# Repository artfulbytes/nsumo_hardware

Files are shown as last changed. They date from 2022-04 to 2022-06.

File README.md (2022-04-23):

# Nsumo hardware
This repository contains the schematic and PCB design of Nsumo, a mini-class Sumobot (500g 10x10cm),
created in KiCad, and manufactured by JLCPCB. It's a 2-layer PCB with microcontroller MSP430G2553IPW28,
regulators 3.3V (AMS1117-3.3) and 5V (MP2359), two motor drivers TB6612FNG, IR receiver TSP382, and
circuit protection (RS3E075AT).

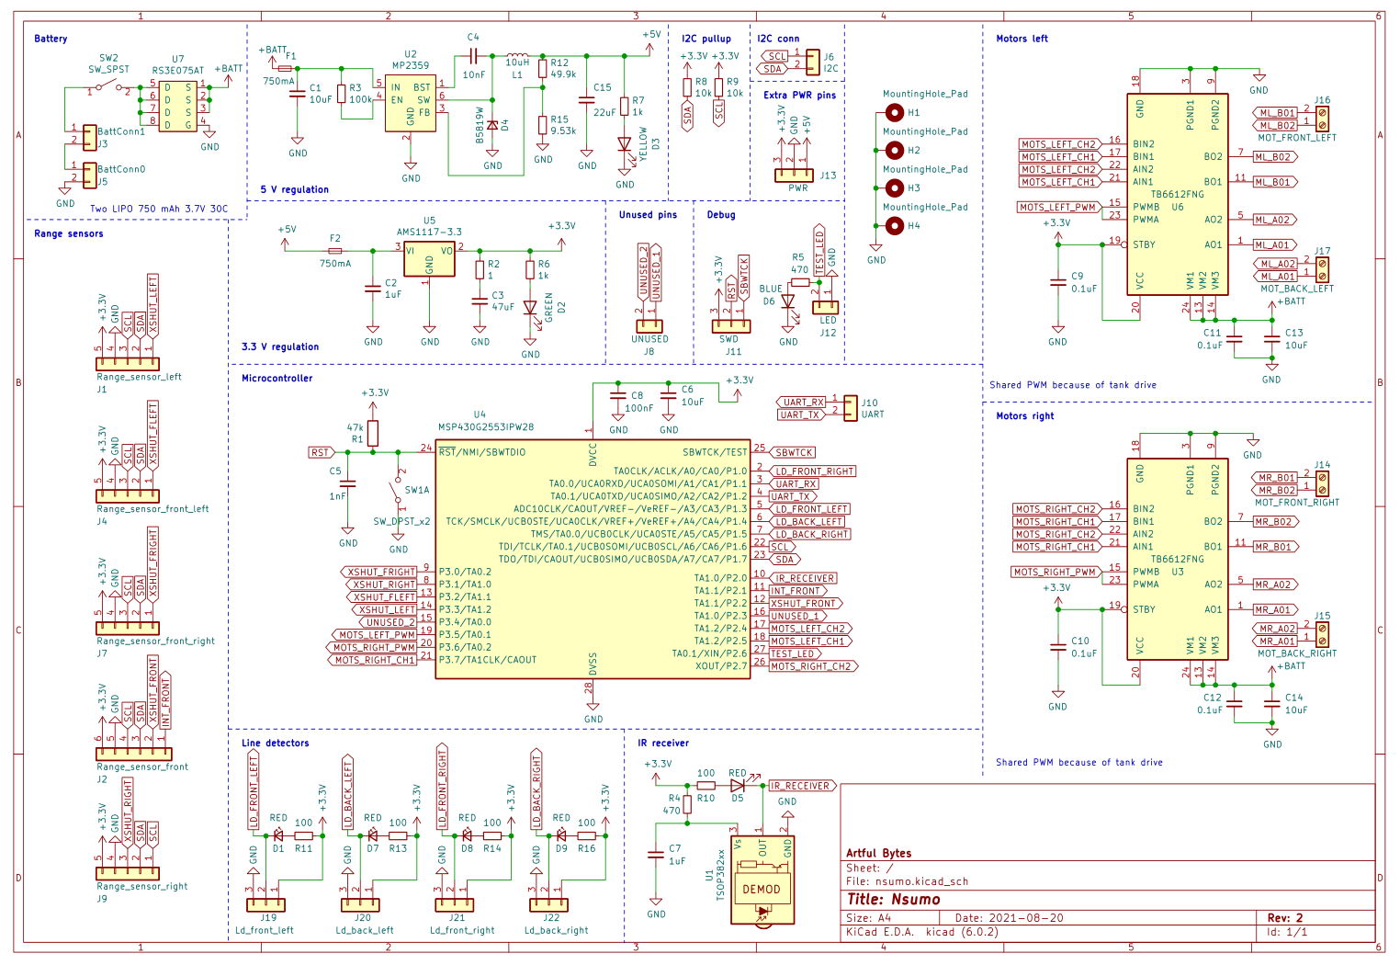
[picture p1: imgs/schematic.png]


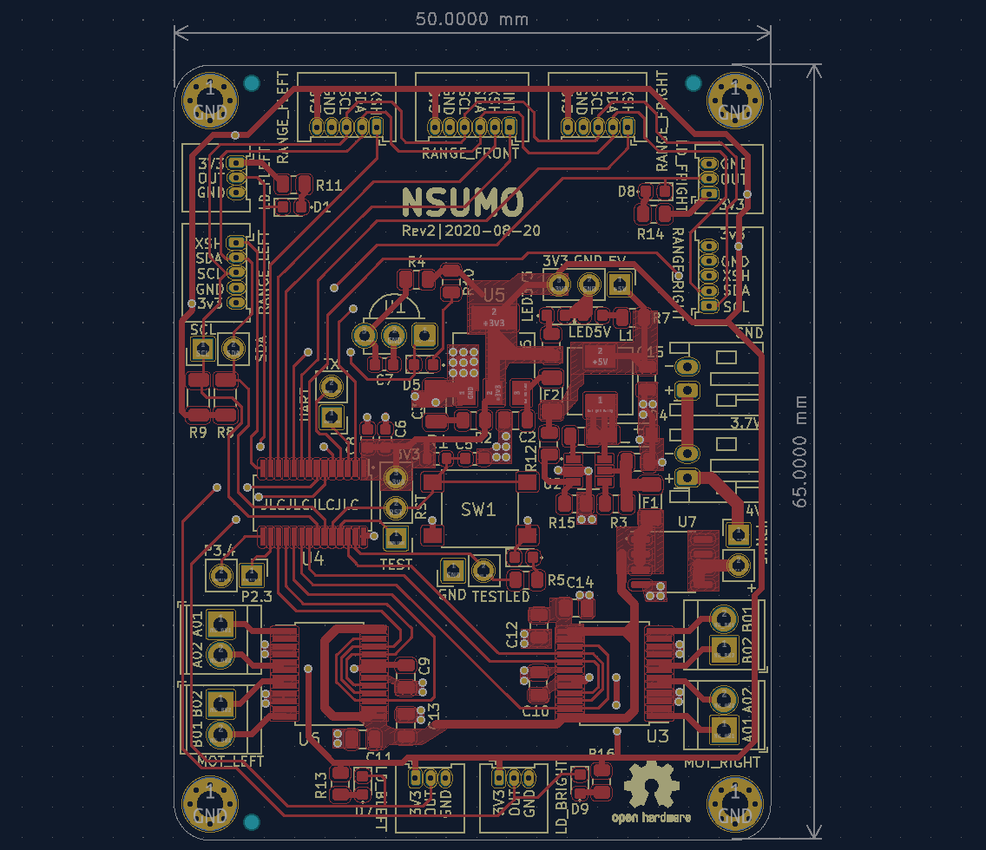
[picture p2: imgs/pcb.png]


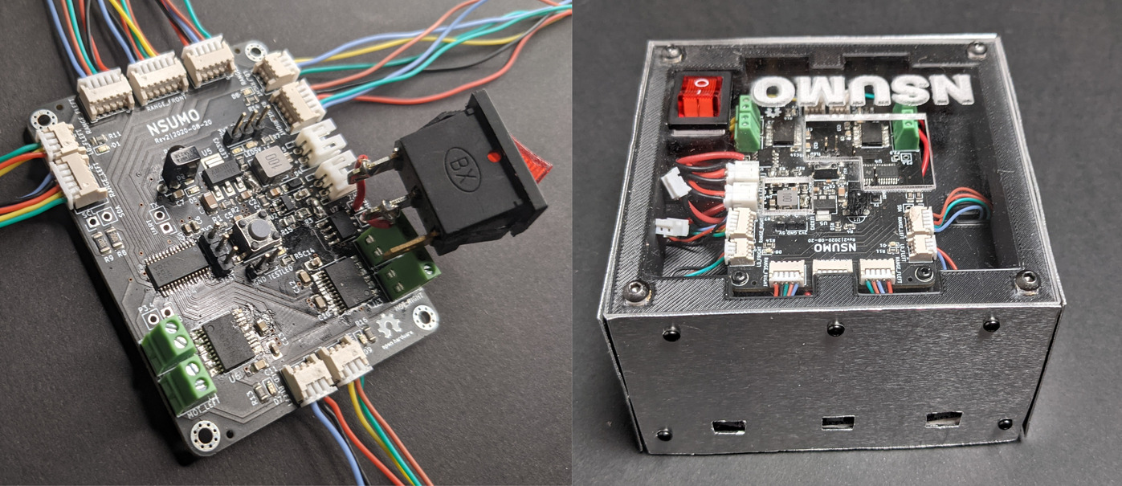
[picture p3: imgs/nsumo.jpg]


## Setup
Import the project into KiCad >6.0 and make sure you have the "default global symbol library table"
and the "default footprint library" available. KiCad should find the 3Dmodels and symbols under _libs/_
automatically. You must manually import the footprints under _libs/footprints/_ (select "file/add library"
from the menu in the footprint editor and add them to the project).

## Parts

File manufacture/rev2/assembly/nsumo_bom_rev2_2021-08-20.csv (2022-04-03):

Comment | Designator | Footprint | LCSC Part #
10uF Unpolarized capacitor, small symbol | C13,C14,C1,C6 | C_0603_1608Metric | C19702
22uF Unpolarized capacitor, small symbol | C15 | C_0805_2012Metric | C45783
47uF Unpolarized capacitor, small symbol | C3 | C_1206_3216Metric | C96123
10nF Unpolarized capacitor, small symbol | C4 | C_0805_2012Metric | C1710
1nF Unpolarized capacitor, small symbol | C5 | C_0603_1608Metric | C1588
1uF Unpolarized capacitor, small symbol | C7,C2 | C_0805_2012Metric | C28323
100nF Unpolarized capacitor, small symbol | C8 | C_0603_1608Metric | C14663
0.1uF Unpolarized capacitor, small symbol | C9,C11,C12,C10 | C_0805_2012Metric | C49678
GREEN Light emitting diode | D2 | LED_0603_1608Metric | C72043
YELLOW Light emitting diode | D3 | LED_0603_1608Metric | C72038
B5819W Zener diode, small symbol | D4 | D_SOD-123 | C8598
RED Light emitting diode | D5 | LED_0603_1608Metric | C2286
BLUE Light emitting diode | D6 | LED_0603_1608Metric | C72041
RED Light emitting diode, small symbol | D7,D8,D9,D1 | LED_0603_1608Metric | C2286
750mA Fuse, small symbol | F2,F1 | Fuse_1206_3216Metric
MountingHole_Pad Mounting Hole with connection | H1,H2,H3,H4 | MountingHole_2.2mm_M2_Pad_Via
Range_sensor_left Generic connector, single row, 01x05, script generated (kicad-library-utils/schlib/autogen/connector/) | J1 | Molex_PicoBlade_53048-0510_1x05_P1.25mm_Horizontal
UART Generic connector, single row, 01x02, script generated (kicad-library-utils/schlib/autogen/connector/) | J10 | PinHeader_1x02_P2.54mm_Vertical
SWD Generic connector, single row, 01x03, script generated (kicad-library-utils/schlib/autogen/connector/) | J11 | PinHeader_1x03_P2.54mm_Vertical
LED Generic connector, single row, 01x02, script generated (kicad-library-utils/schlib/autogen/connector/) | J12 | PinHeader_1x02_P2.54mm_Vertical
PWR Generic connector, single row, 01x03, script generated (kicad-library-utils/schlib/autogen/connector/) | J13 | PinHeader_1x03_P2.54mm_Vertical
MOT_FRONT_RIGHT Generic screw terminal, single row, 01x02, script generated (kicad-library-utils/schlib/autogen/connector/) | J14 | TerminalBlock_TE_282834-2_1x02_P2.54mm_Horizont
MOT_BACK_RIGHT Generic screw terminal, single row, 01x02, script generated (kicad-library-utils/schlib/autogen/connector/) | J15 | TerminalBlock_TE_282834-2_1x02_P2.54mm_Horizont
MOT_FRONT_LEFT Generic screw terminal, single row, 01x02, script generated (kicad-library-utils/schlib/autogen/connector/) | J16 | TerminalBlock_TE_282834-2_1x02_P2.54mm_Horizont
MOT_BACK_LEFT Generic screw terminal, single row, 01x02, script generated (kicad-library-utils/schlib/autogen/connector/) | J17 | TerminalBlock_TE_282834-2_1x02_P2.54mm_Horizont
Ld_front_left Generic connector, single row, 01x03, script generated (kicad-library-utils/schlib/autogen/connector/) | J19 | Molex_PicoBlade_53048-0310_1x03_P1.25mm_Horizontal
Range_sensor_front Generic connector, single row, 01x06, script generated (kicad-library-utils/schlib/autogen/connector/) | J2 | Molex_PicoBlade_53048-0610_1x06_P1.25mm_Horizontal
Ld_back_left Generic connector, single row, 01x03, script generated (kicad-library-utils/schlib/autogen/connector/) | J20 | Molex_PicoBlade_53048-0310_1x03_P1.25mm_Horizontal
Ld_front_right Generic connector, single row, 01x03, script generated (kicad-library-utils/schlib/autogen/connector/) | J21 | Molex_PicoBlade_53048-0310_1x03_P1.25mm_Horizontal
Ld_back_right Generic connector, single row, 01x03, script generated (kicad-library-utils/schlib/autogen/connector/) | J22 | Molex_PicoBlade_53048-0310_1x03_P1.25mm_Horizontal
BattConn1 Generic connector, single row, 01x02, script generated (kicad-library-utils/schlib/autogen/connector/) | J3 | JST_PH_S2B-PH-K_1x02_P2.00mm_Horizontal
Range_sensor_front_left Generic connector, single row, 01x05, script generated (kicad-library-utils/schlib/autogen/connector/) | J4 | Molex_PicoBlade_53048-0510_1x05_P1.25mm_Horizontal
BattConn0 Generic connector, single row, 01x02, script generated (kicad-library-utils/schlib/autogen/connector/) | J5 | JST_PH_S2B-PH-K_1x02_P2.00mm_Horizontal
I2C Generic connector, single row, 01x02, script generated (kicad-library-utils/schlib/autogen/connector/) | J6 | PinHeader_1x02_P2.54mm_Vertical
Range_sensor_front_right Generic connector, single row, 01x05, script generated (kicad-library-utils/schlib/autogen/connector/) | J7 | Molex_PicoBlade_53048-0510_1x05_P1.25mm_Horizontal
UNUSED Generic connector, single row, 01x02, script generated (kicad-library-utils/schlib/autogen/connector/) | J8 | PinHeader_1x02_P2.54mm_Vertical
Range_sensor_right Generic connector, single row, 01x05, script generated (kicad-library-utils/schlib/autogen/connector/) | J9 | Molex_PicoBlade_53048-0510_1x05_P1.25mm_Horizontal
10uH Inductor, small symbol | L1 | L_Sunlord_MWSA0518_5.4x5.2mm | C408412
47k Resistor | R1 | R_0603_1608Metric | C25819
49.9k Resistor, small symbol | R12 | R_0805_2012Metric | C17719
100 Resistor, small symbol | R13,R14,R16,R11,R10 | R_0805_2012Metric | C17408
9.53k Resistor, small symbol | R15 | R_0805_2012Metric
1 Resistor, small symbol | R2 | R_0805_2012Metric | C25271
100k Resistor, small symbol | R3 | R_0805_2012Metric | C17407
470 Resistor, small symbol | R5,R4 | R_0805_2012Metric | C17710
1k Resistor, small symbol | R6,R7 | R_0805_2012Metric | C17513
10k Resistor, small symbol | R8,R9 | R_1206_3216Metric | C17902
SW_DPST_x2 Single Pole Single Throw (SPST) switch, separate symbol | SW1 | SW_Push_1P1T_NO_6x6mm_H9.5mm
SW_SPST Single Pole Single Throw (SPST) switch | SW2 | PinHeader_1x02_P2.54mm_Vertical
TSOP382xx Photo Modules for PCM Remote Control Systems | U1 | Vishay_MINICAST-3Pin
MP2359 | U2 | TSOT-23-6
MSP430G2553IPW28 1kB Flash, 256B RAM, TSSOP-28 | U4 | TSSOP-28_4.4x9.7mm_P0.65mm
AMS1117-3.3 1A Low Dropout regulator, positive, 1.5V fixed output, SOT-223 | U5 | SOT-223-3_TabPin2 | C6186
TB6612FNG Driver IC for Dual DC motor, SSOP-24 | U6,U3 | SSOP-24_5.3x8.2mm_P0.65mm_LongPads
RS3E075AT | U7 | SOP-8_3.9x4.9mm_P1.27mm

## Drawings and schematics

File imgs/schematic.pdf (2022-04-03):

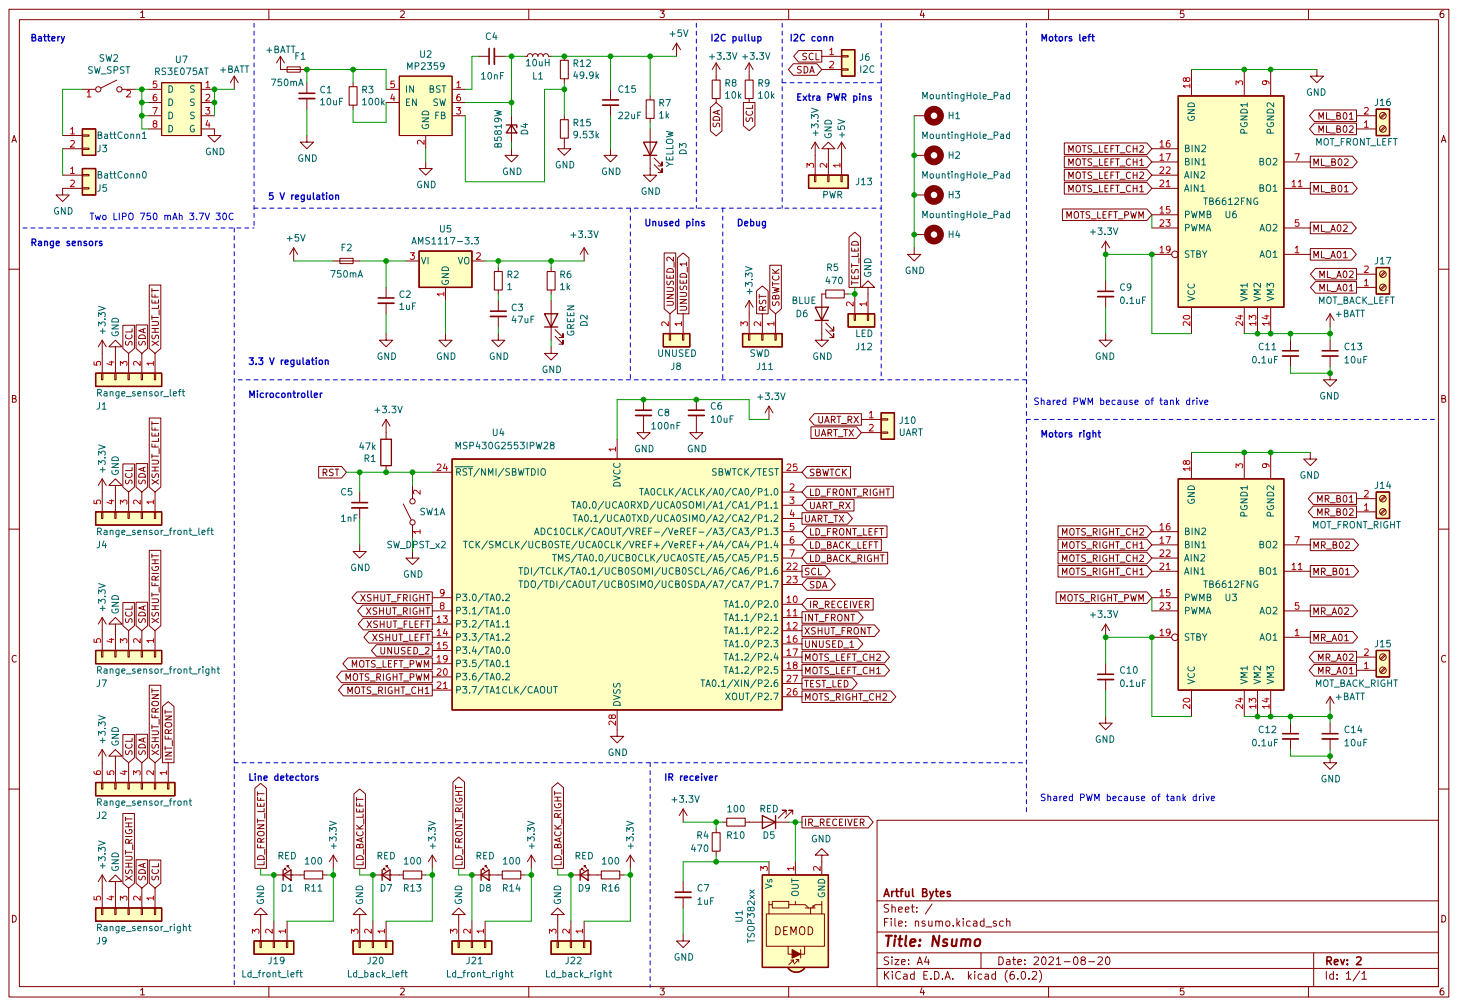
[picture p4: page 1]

Shared PWM because of tank drive Motors right

File: nsumo.kicad_sch Sheet: / Artful Bytes

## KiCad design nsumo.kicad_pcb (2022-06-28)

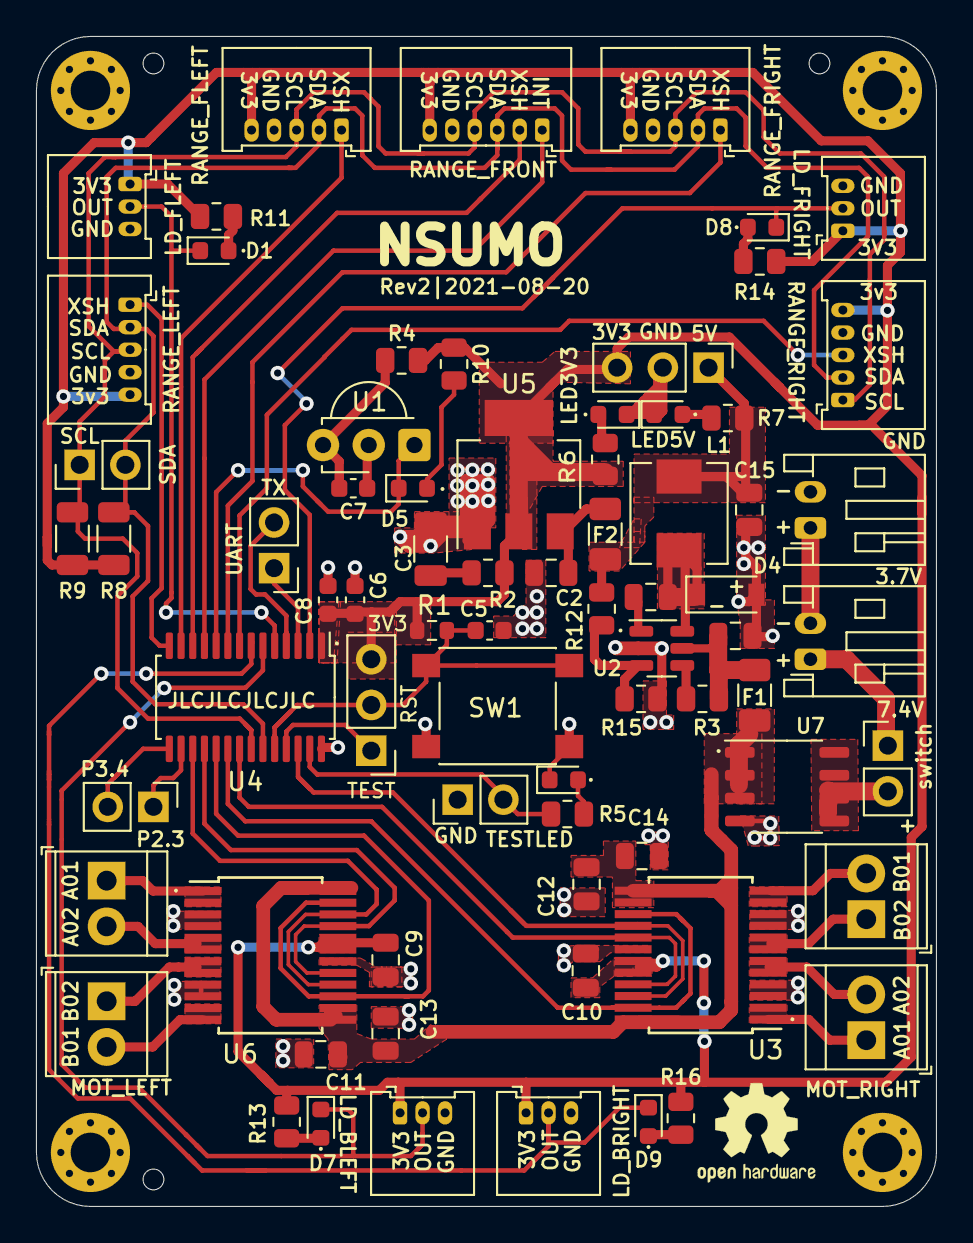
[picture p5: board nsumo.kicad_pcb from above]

Board: 2 copper layers, 50.0 x 65.0 mm, 77 parts (0 on the bottom side), 57 nets.

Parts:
C1, C13, C14: 10uF; C_0805_2012Metric
C2: 1uF; C_0805_2012Metric
C3: 47uF; C_1206_3216Metric
C4: 10nF; C_0805_2012Metric
C5: 1nF; C_0603_1608Metric
C6: 10uF; C_0603_1608Metric
C7: 1uF; C_0603_1608Metric
C8: 100nF; C_0603_1608Metric
C9, C10, C11, C12: 0.1uF; C_0805_2012Metric
C15: 22uF; C_0805_2012Metric
D1, D5, D7, D8, D9: RED; LED_0603_1608Metric
D2: GREEN; LED_0603_1608Metric
D3: YELLOW; LED_0603_1608Metric
D4: B5819W; D_SOD-123
D6: BLUE; LED_0603_1608Metric
F1, F2: 750mA; Fuse_1206_3216Metric
H1, H2, H3, H4: MountingHole_Pad; MountingHole_2.2mm_M2_Pad_Via
J1: Range_sensor_left; Molex_PicoBlade_53048-0510_1x05_P1.25mm_Horizontal
J2: Range_sensor_front; Molex_PicoBlade_53048-0610_1x06_P1.25mm_Horizontal
J3: BattConn1; JST_PH_S2B-PH-K_1x02_P2.00mm_Horizontal
J4: Range_sensor_front_left; Molex_PicoBlade_53048-0510_1x05_P1.25mm_Horizontal
J5: BattConn0; JST_PH_S2B-PH-K_1x02_P2.00mm_Horizontal
J6: I2C; PinHeader_1x02_P2.54mm_Vertical
J7: Range_sensor_front_right; Molex_PicoBlade_53048-0510_1x05_P1.25mm_Horizontal
J8: UNUSED; PinHeader_1x02_P2.54mm_Vertical
J9: Range_sensor_right; Molex_PicoBlade_53048-0510_1x05_P1.25mm_Horizontal
J10: UART; PinHeader_1x02_P2.54mm_Vertical
J11: SWD; PinHeader_1x03_P2.54mm_Vertical
J12: LED; PinHeader_1x02_P2.54mm_Vertical
J13: PWR; PinHeader_1x03_P2.54mm_Vertical
J14: MOT_FRONT_RIGHT; TerminalBlock_TE_282834-2_1x02_P2.54mm_Horizont
J15: MOT_BACK_RIGHT; TerminalBlock_TE_282834-2_1x02_P2.54mm_Horizont
J16: MOT_FRONT_LEFT; TerminalBlock_TE_282834-2_1x02_P2.54mm_Horizont
J17: MOT_BACK_LEFT; TerminalBlock_TE_282834-2_1x02_P2.54mm_Horizont
J19: Ld_front_left; Molex_PicoBlade_53048-0310_1x03_P1.25mm_Horizontal
J20: Ld_back_left; Molex_PicoBlade_53048-0310_1x03_P1.25mm_Horizontal
J21: Ld_front_right; Molex_PicoBlade_53048-0310_1x03_P1.25mm_Horizontal
J22: Ld_back_right; Molex_PicoBlade_53048-0310_1x03_P1.25mm_Horizontal
L1: 10uH; L_Sunlord_MWSA0518_5.4x5.2mm
R1: 47k; R_0603_1608Metric
R2: 1; R_0805_2012Metric
R3: 100k; R_0805_2012Metric
R4, R5: 470; R_0805_2012Metric
R6, R7: 1k; R_0805_2012Metric
R8, R9: 10k; R_1206_3216Metric
R10, R11, R13, R14, R16: 100; R_0805_2012Metric
R12: 49.9k; R_0805_2012Metric
R15: 9.53k; R_0805_2012Metric
SW1: SW_DPST_x2; SW_Push_1P1T_NO_6x6mm_H9.5mm
SW2: SW_SPST; PinHeader_1x02_P2.54mm_Vertical
U1: TSOP382xx; Vishay_MINICAST-3Pin
U2: MP2359; TSOT-23-6
U3, U6: TB6612FNG; SSOP-24_5.3x8.2mm_P0.65mm_LongPads
U4: MSP430G2553IPW28; TSSOP-28_4.4x9.7mm_P0.65mm
U5: AMS1117-3.3; SOT-223-3_TabPin2
U7: RS3E075AT; SOP-8_3.9x4.9mm_P1.27mm

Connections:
+3V3: C6.1, C8.1, C9.1, C10.1, J1.5, J2.6, J4.5, J7.5, J9.5, J11.3, J13.3, J19.1, J20.1, J21.1, J22.1, R1.2, R2.1, R4.2, R6.1, R8.1, R9.1, R10.1, R11.1, R13.1, R14.1, R16.1, U3.19, U3.20, U4.1, U5.2, U6.19, U6.20
+5V: C15.1, F2.1, J13.1, L1.2, R7.1, R12.1
+BATT: C11.1, C12.1, C13.1, C14.1, F1.1, U3.13, U3.14, U3.24, U6.13, U6.14, U6.24, U7.1, U7.2, U7.3
GND: C1.2, C2.2, C3.2, C5.2, C6.2, C7.2, C8.2, C9.2, C10.2, C11.2, C12.2, C13.2, C14.2, C15.2, D2.1, D3.1, D4.2, D6.1, H1.1, H2.1, H3.1, H4.1, J1.4, J2.5, J4.4, J5.2, J7.4, J9.4, J12.1, J13.2, J19.3, J20.3, J21.3, J22.3, R15.2, SW1.1, U1.2, U2.2, U3.3, U3.4, U3.9, U3.10, U3.18, U4.28, U5.1, U6.3, U6.4, U6.9, U6.10, U6.18, U7.4
INT_FRONT: J2.1, U4.11
IR_RECEIVER: D5.1, U1.1, U4.10
LD_BACK_LEFT: D7.1, J20.2, U4.6
LD_BACK_RIGHT: D9.1, J22.2, U4.7
LD_FRONT_LEFT: D1.1, J19.2, U4.5
LD_FRONT_RIGHT: D8.1, J21.2, U4.2
ML_A01: J17.1, U6.1, U6.2
ML_A02: J17.2, U6.5, U6.6
ML_B01: J16.2, U6.11, U6.12
ML_B02: J16.1, U6.7, U6.8
MOTS_LEFT_CH1: U4.18, U6.17, U6.21
MOTS_LEFT_CH2: U4.17, U6.16, U6.22
MOTS_LEFT_PWM: U4.19, U6.15, U6.23
MOTS_RIGHT_CH1: U3.17, U3.21, U4.21
MOTS_RIGHT_CH2: U3.16, U3.22, U4.26
MOTS_RIGHT_PWM: U3.15, U3.23, U4.20
MR_A01: J15.1, U3.1, U3.2
MR_A02: J15.2, U3.5, U3.6
MR_B01: J14.2, U3.11, U3.12
MR_B02: J14.1, U3.7, U3.8
unnamed: C1.1, F1.2, R3.1, U2.5
unnamed: C2.1, F2.2, U5.3
unnamed: C3.1, R2.2
unnamed: C4.1, U2.1
unnamed: C4.2, D4.1, L1.1, U2.6
unnamed: C7.1, R4.1, U1.3
unnamed: D1.2, R11.2
unnamed: D2.2, R6.2
unnamed: D3.2, R7.2
unnamed: D5.2, R10.2
unnamed: D6.2, R5.2
unnamed: D7.2, R13.2
unnamed: D8.2, R14.2
unnamed: D9.2, R16.2
unnamed: J3.1, SW2.1
unnamed: J3.2, J5.1
unnamed: R3.2, U2.4
unnamed: R12.2, R15.1, U2.3
unnamed: SW2.2, U7.5, U7.6, U7.7, U7.8
RST: C5.1, J11.2, R1.1, SW1.2, U4.24
SBWTCK: J11.1, U4.25
SCL: J1.3, J2.4, J4.3, J6.1, J7.3, J9.1, R9.2, U4.22
SDA: J1.2, J2.3, J4.2, J6.2, J7.2, J9.2, R8.2, U4.23
TEST_LED: J12.2, R5.1, U4.27
UART_RX: J10.1, U4.3
UART_TX: J10.2, U4.4
UNUSED_1: J8.1, U4.16
UNUSED_2: J8.2, U4.15
XSHUT_FLEFT: J4.1, U4.13
XSHUT_FRIGHT: J7.1, U4.9
XSHUT_FRONT: J2.2, U4.12
XSHUT_LEFT: J1.1, U4.14
XSHUT_RIGHT: J9.3, U4.8

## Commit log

2021-06-13 NEW: Add files for the first time
    Only stored the files locally until now...
    [nsumo-B_Cu.gbr, nsumo-B_Mask.gbr, nsumo-B_Paste.gbr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]
2021-06-15 FIX: Change PTC fuse footprint from 0805 to 1206
    There are more ones available in 1206 at Digi-Key.
    [nsumo-B_Cu.gbr, nsumo-B_Mask.gbr, nsumo-B_Paste.gbr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]
2021-07-17 FIX: Add missing datasheets to BOM
    [nsumo.sch]
2022-04-03 ENH: REV2
    First revision had several issues. Fix these for
    revision 2.
    [nsumo.kicad_pcb, nsumo.sch]
2022-04-03 Move revision files
    [nsumo-B_Cu.gbr, nsumo-B_Mask.gbr, nsumo-B_Paste.gbr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]
2022-04-03 NEW: REV2 files
    [nsumo-B_Cu.gbr, nsumo-B_Mask.gbr, nsumo-B_Paste.gbr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]
2022-04-03 FIX: Small updates to README
    [nsumo.kicad_pcb, nsumo.sch]
2022-04-23 ENH: Update the project for KiCad 6.0
    Make the project compatible with KiCad 6.0 and add some notes
    about importing it.
    [nsumo.kicad_pcb, nsumo.kicad_sch, nsumo.sch]
2022-06-28 FIX: Add missing 3D models
    * Button switch
    * Inductor
    * Mosfet
    * Motor drivers
    [nsumo.kicad_pcb]
